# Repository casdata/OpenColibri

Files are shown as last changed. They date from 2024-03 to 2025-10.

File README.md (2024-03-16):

# OpenColibri
Control board for the Necta Colibri vending machine + firmware

The OpenColibri project is an alternative solution for the Colibri - Necta coffee machines with a damaged main board, enabling all the features except for the stirrer dispensing unit and the cup dispenser unit.

The board features an ESP32 MCU, programmed over ESP-IDF. 

There are 13 available recipe slots to program and choose from. The button #8 works as a page changer, when pressed the current page changes, giving access to the rest of the recipe slots. In total, there are 2 pages, seven recipes are available on the first page and six on the second page, in this last one, push button #7 works as a manual hot water outlet switch, pressing it will toggle the hot water outlet.

Button #8 cancels the selected recipe preparation only while the grinder is working, after this, the preparation can’t be canceled.

<p align="center">
  
</p>

## Board
Front            |  Back
:-------------------------:|:-------------------------:
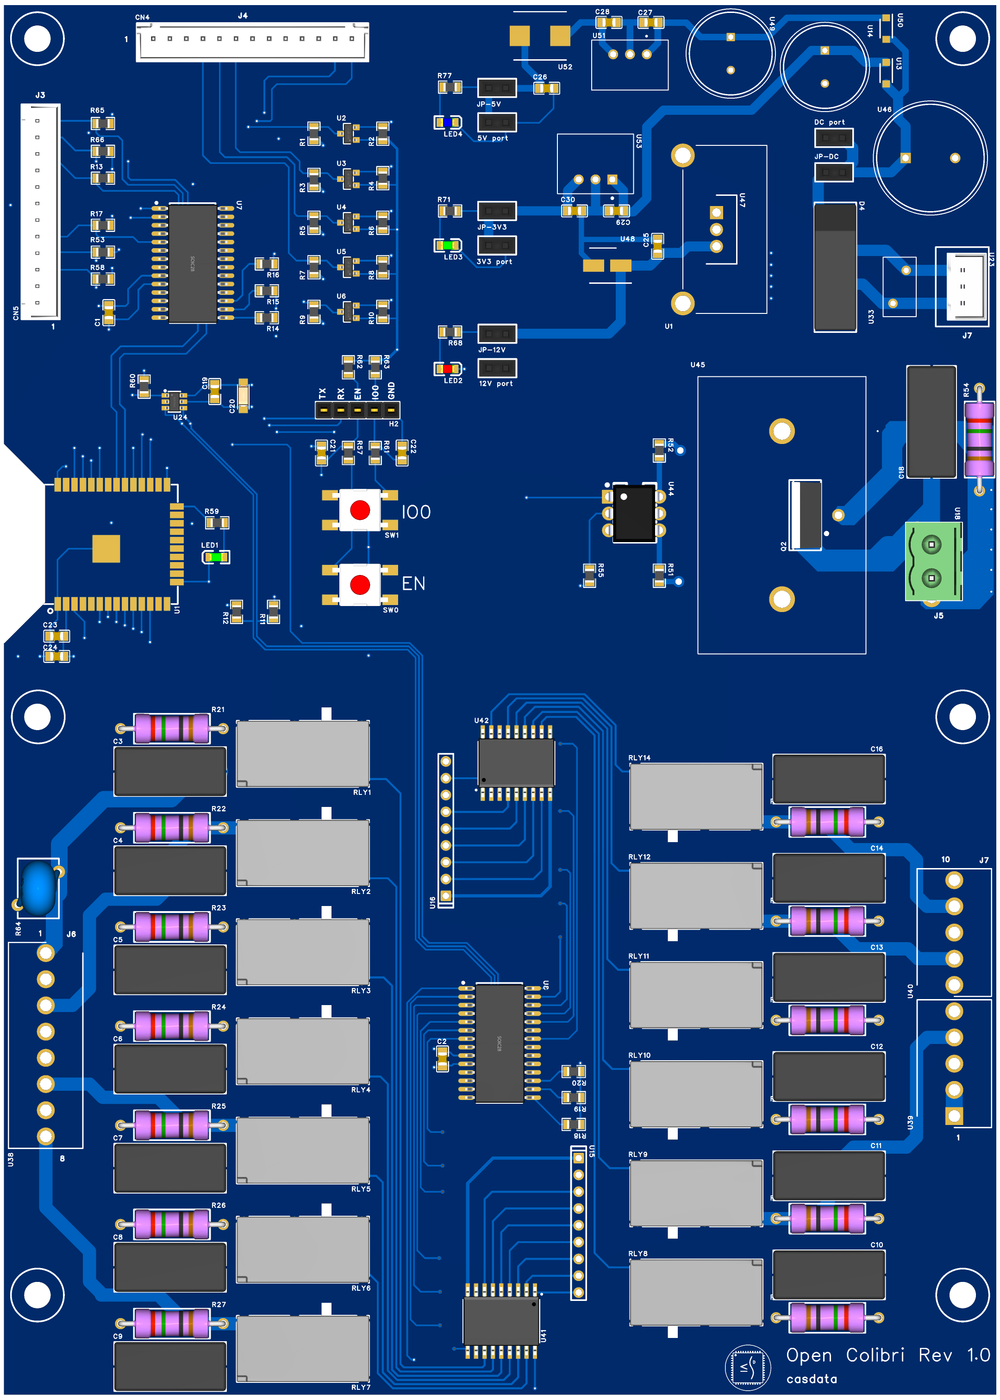
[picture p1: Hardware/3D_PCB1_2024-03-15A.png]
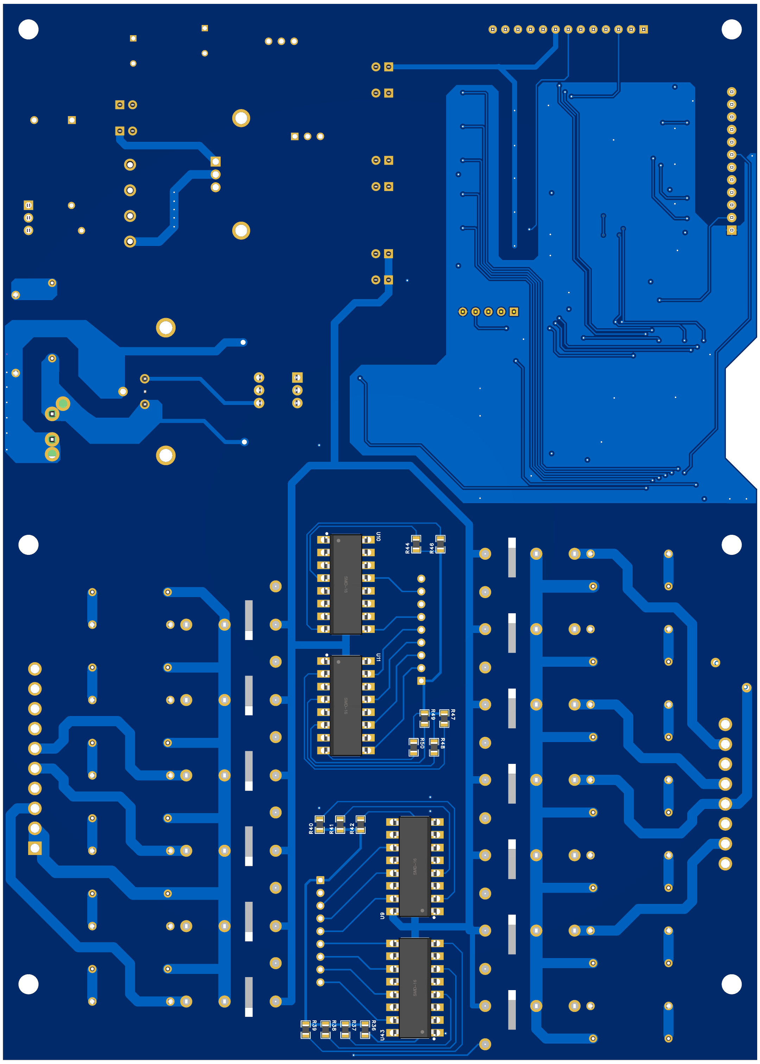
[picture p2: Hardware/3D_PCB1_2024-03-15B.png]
  |  

## Schematic Diagram
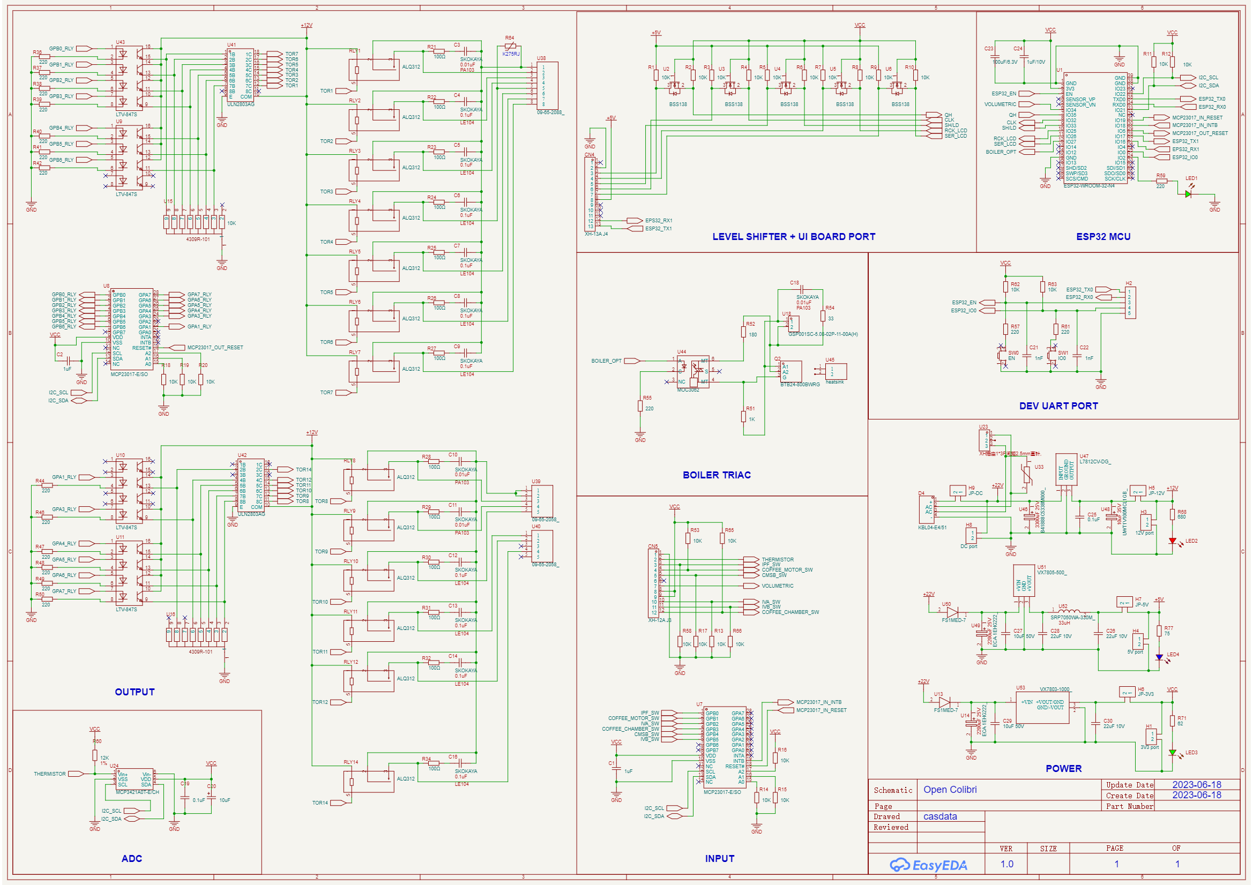
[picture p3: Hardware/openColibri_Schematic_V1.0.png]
Schematic
     

## Android App
To create and assign recipes to the recipe slots, the App “OpenColibri” for Android (Android 12 and lesser) is available for this task, it communicates with the machine through BLE (Bluetooth Low Energy). Download APK <a href="Android App/android-release.apk">Here</a>

  <p align="center">
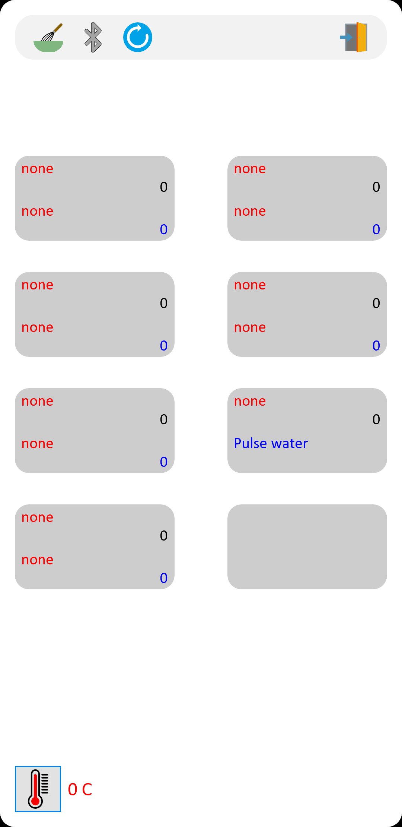
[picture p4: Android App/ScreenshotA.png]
    
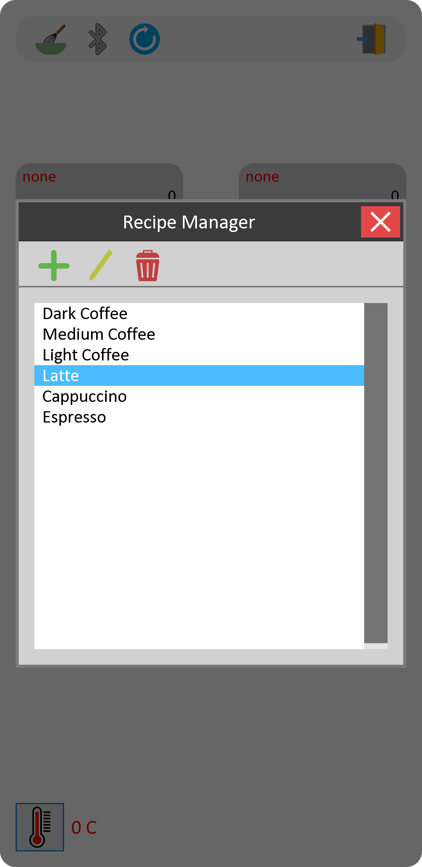
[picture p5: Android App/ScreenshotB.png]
    
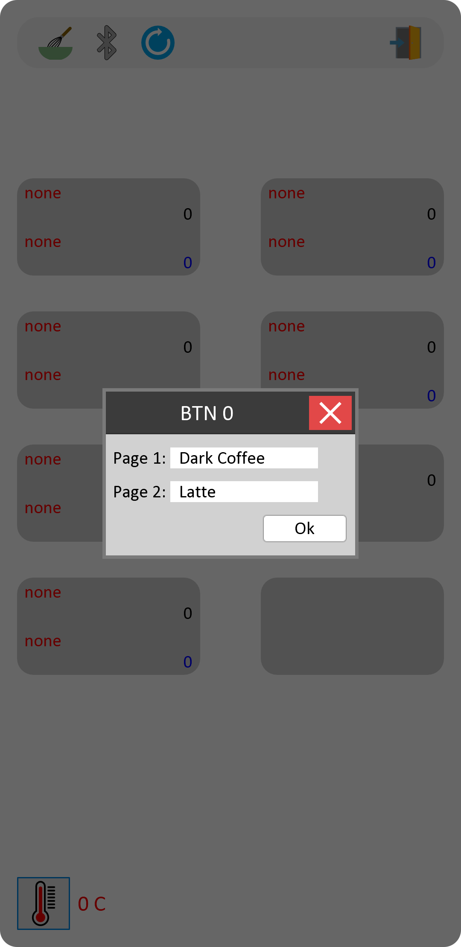
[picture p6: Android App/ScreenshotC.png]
    
  </p>

  The app is in Beta version, it works and it’s functional. It's normal to find some crash bugs. Don’t assign any recipe to the buttons or press the synchronize or boiler buttons before the App and the machine is synchronized, otherwise, it will crash.

  <h3>Connect to the App</h3>
<ul type="1">
  <li>Press the “Washing cycle” button in the machine, and the word “MAINTENANCE” will be displayed, button #1 will enable the BLE of the ESP32, and once pressed, the message “Bluetooth ON” will be displayed.</li>
  <li>Open the App on your Android device, press the Bluetooth icon, connect to the “OpenColibri”, press the synchronize button (the blue circle with the arrow), and wait a few seconds.</li>
  <li>After synchronization is done, any change made in the app will automatically sent to the machine.</li>
</ul>

## Washing Button
The original washing button of the machine is used for a basic maintenance menu, after pressed, it will show "MAINTENANCE" in the display.
<ul>
  <li>Button #1: Enables Bluetooth</li>
  <li>Button #5: Washing cycle</li>
  <li>Button #7: Exit maintenance menu</li>
</ul>

## Contact

Sergio Daniel Castañeda N. - [@twitter_handle](https://twitter.com/CasdataSergio) - casdata@gmail.com

Website: http://casnisoft.weebly.com

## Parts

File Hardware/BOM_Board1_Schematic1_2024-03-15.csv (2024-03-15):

No. | Quantity | Comment | Designator | Footprint | Value | Manufacturer Part | Manufacturer | Supplier Part | Supplier
1 | 2 | 1uF | C1,C2 | C0805 | 1uF
2 | 14 | SKOKAYA | C3,C4,C5,C6,C7,C8,C9,C10,C11,C12,C13,C14,C16,C18 | CAP-TH_L16.9-W7.4-P15.00-D0.6 |  | SKOKAYA |  | C9900019984 | LCSC
3 | 2 | 0.1uF | C19,C25 | C0805 | 0.1uF
4 | 1 | 10uF | C20 | CAP-SMD_L3.2-W1.6-RD-C7171 | 10uF | TAJA106K016RNJ | Kyocera AVX | C7171 | LCSC
5 | 2 | 1nF | C21,C22 | C0805 | 1nF
6 | 1 | 100uF/6.3V | C23 | C0805 | 100uF/6.3V
7 | 1 | 1uF/10V | C24 | C0805 | 1uF/10V
8 | 3 | 22uF 10V | C26,C28,C30 | C0805 | 22uF 10V
9 | 2 | 10uF 50V | C27,C29 | C0805 | 10uF 50V
10 | 1 | XH-13A J4 | CN4 | CONN-TH_13P-P2.50_XH-13A |  | XH-13A | BOOMELE(博穆精密) | C40669 | LCSC
11 | 1 | XH-12A J3 | CN5 | CONN-TH_12P-P2.50_HCTL_XH-12A_C2908610 |  | XH-12A | HCTL(华灿天禄) | C2908610 | LCSC
12 | 1 | KBL04-E4/51 | D4 | KBL_4P-L19.0-W6.3-P5.10 |  | KBL04-E4/51 | VISHAY(威世) | C145346 | LCSC
13 | 1 | 3V3 port | H1 | HDR-TH_2P-P2.54-V-F
14 | 1 | HDR-F_2.54_1x5P | H2 | HDR-TH_5P-P2.54-V-F
15 | 1 | 12V port | H3 | HDR-TH_2P-P2.54-V-F
16 | 1 | 5V port | H4 | HDR-TH_2P-P2.54-V-F
17 | 1 | JP-12V | H5 | HDR-TH_2P-P2.54-V-F
18 | 1 | JP-3V3 | H6 | HDR-TH_2P-P2.54-V-F
19 | 1 | JP-5V | H7 | HDR-TH_2P-P2.54-V-F
20 | 1 | DC port | H8 | HDR-TH_2P-P2.54-V-F
21 | 1 | JP-DC | H9 | HDR-TH_2P-P2.54-V-F
22 | 2 | LED_0805-G | LED1,LED3 | LED0805-RD_GREEN
23 | 1 | LED_0805-R | LED2 | LED0805-RD_GREEN
24 | 1 | LED_0805-B | LED4 | LED0805-RD_GREEN
25 | 1 | BTB24-800BWRG | Q2 | TO-220-3_L10.0-W4.5-P2.54-L |  | BTB24-800BWRG | ST(意法半导体) | C262877 | LCSC
26 | 26 | 10K | R1,R2,R3,R4,R5,R6,R7,R8,R9,R10,R11,R12,R13,R14,R15,R16,R17,R18,R19,R20,R53,R58,R62,R63,R65,R66 | R0805 | 10K
27 | 13 | 100Ω | R21,R22,R23,R24,R25,R26,R27,R28,R29,R30,R31,R32,R34 | RES-TH_BD4.5-L11.5-P15.50-D0.8 | 100Ω
28 | 17 | 220 | R36,R37,R38,R39,R40,R41,R42,R44,R46,R47,R48,R49,R50,R55,R57,R59,R61 | R0805 | 220
29 | 1 | 1K | R51 | R0805 | 1K
30 | 1 | 180 | R52 | R0805 | 180
31 | 1 | 33 | R54 | RES-TH_BD4.5-L11.5-P15.50-D0.8 | 33
32 | 1 | 12K | R60 | R0805 | 12K
33 | 1 | FTR07D781K | R64 | RES-TH_L9.0-W6.2-P5.00-D0.7-S6.20 |  | FTR07D781K | FTR(乔光电子) | C693590 | LCSC
34 | 1 | 680 | R68 | R0805 | 680
35 | 1 | 62 | R71 | R0805 | 62
36 | 1 | 75 | R77 | R0805 | 75
37 | 13 | ALQ312 | RLY1,RLY2,RLY3,RLY4,RLY5,RLY6,RLY7,RLY8,RLY9,RLY10,RLY11,RLY12,RLY14 | RELAY-TH_ALQ3XX |  | ALQ312 | PANASONIC(松下) | C425093 | LCSC
38 | 1 | EN | SW0 | SW-SMD_4P-L6.0-W6.0-P4.50-LS9.0-2
39 | 1 | IO0 | SW1 | SW-SMD_4P-L6.0-W6.0-P4.50-LS9.0-2
40 | 1 | ESP32-WROOM-32-N4 | U1 | WIFIM-SMD_ESP32-WROOM-32-N4 |  | ESP32-WROOM-32-N4 | ESPRESSIF(乐鑫) | C82899 | LCSC
41 | 5 | BSS138 | U2,U3,U4,U5,U6 | SOT-23_L2.9-W1.3-P1.90-LS2.4-BR |  | BSS138 | JUXING(钜兴) | C5279927 | LCSC
42 | 2 | MCP23017-E/SO | U7,U8 | SOIC-28_L18.0-W7.5-P1.27-LS10.3-BL |  | MCP23017-E/SO | MICROCHIP(美国微芯) | C47023 | LCSC
43 | 4 | LTV-847S | U9,U10,U11,U43 | OPTO-SMD-16_L19.8-W6.5-P2.54-LS10.2-BL |  | LTV-847S |  | C9900002565 | LCSC
44 | 2 | FS1MED-7 | U13,U50 | SODFL3718X120N
45 | 2 | 423d72adf0cc4111bf5e44c35dbd3aef | U14,U49 | CAPPRD500W65D1250H2700
46 | 1 | 10K | U15 | 4309R-101 9P 2.54
47 | 1 | 4309R-101 | U16 | 4309R-101 9P 2.54
48 | 1 | GSP001SC-5.08-02P-11-00A(H) | U18 | CONN-TH_2P-P5.08_GOOSVN_GSP001SC-5.08-02P-11-00A |  | GSP001SC-5.08-02P-11-00A(H) | GOOSVN(高胜) | C5223769 | LCSC
49 | 1 | XH插座1*3P间距2.5mm直针, | U23 | CONN-TH_C722693 |  | XH插座1*3P间距2.5mm直针, |  | C9900015994 | LCSC
50 | 1 | MCP3421A0T-E/CH | U24 | SOT-23-6_L2.9-W1.6-P0.95-LS2.8-BR |  | MCP3421A0T-E/CH | MICROCHIP(美国微芯) | C29454 | LCSC
51 | 1 | V22ZA1P | U33 | V22ZA1P
52 | 1 | 6dd98926c4964025bade0356167c3037 | U38 | SHDR8W160P0X396_1X8_3092X1062X
53 | 2 | 0ef649be63f348d9a9fb1e8e0b13fae2 | U39,U40 | HDRV5W80P0X396_1X5_1904X1062X1
54 | 2 | ULN2803AG | U41,U42 | SOP-18_L11.5-W7.5-P1.27-LS10.3 |  | ULN2803AG | LANKE(兰科) | C2828556 | LCSC
55 | 1 | MOC3062 | U44 | PDIP-6_L8.5-W6.5-P2.54-LS7.6-BL |  | MOC3062 | LITEON(光宝) | C115473 | LCSC
56 | 1 | heatsink | U45 | 65715ABPE
57 | 1 | f1ad3a9c3df647b5ae5f0771636e6a53 | U46 | CAPPRD750W85D1625H3350
58 | 1 | ed5773b1048145188ff2be5e021da6e6 | U47 | TO255P460X1020X2008-3P
59 | 1 | c534dcd06943492eb338f11ed3634518 | U48 | CAPAE530X550N
60 | 1 | 4b0cc18e117e430396a12b9f0bba2d3b | U51 | VX7805500
61 | 1 | 09b60b7cccee4037ae637b1b8858bb9a | U52 | INDPM7973X540N
62 | 1 | 68940f397d494c0f9dc5991943d3ca98 | U53 | VX78012-1000_VX7803-1000

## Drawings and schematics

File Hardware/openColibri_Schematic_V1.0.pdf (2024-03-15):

# COM 10 8C 11 7C 12 6C 13 5C 14 4C 15 3C 16 2C 17 1C 18

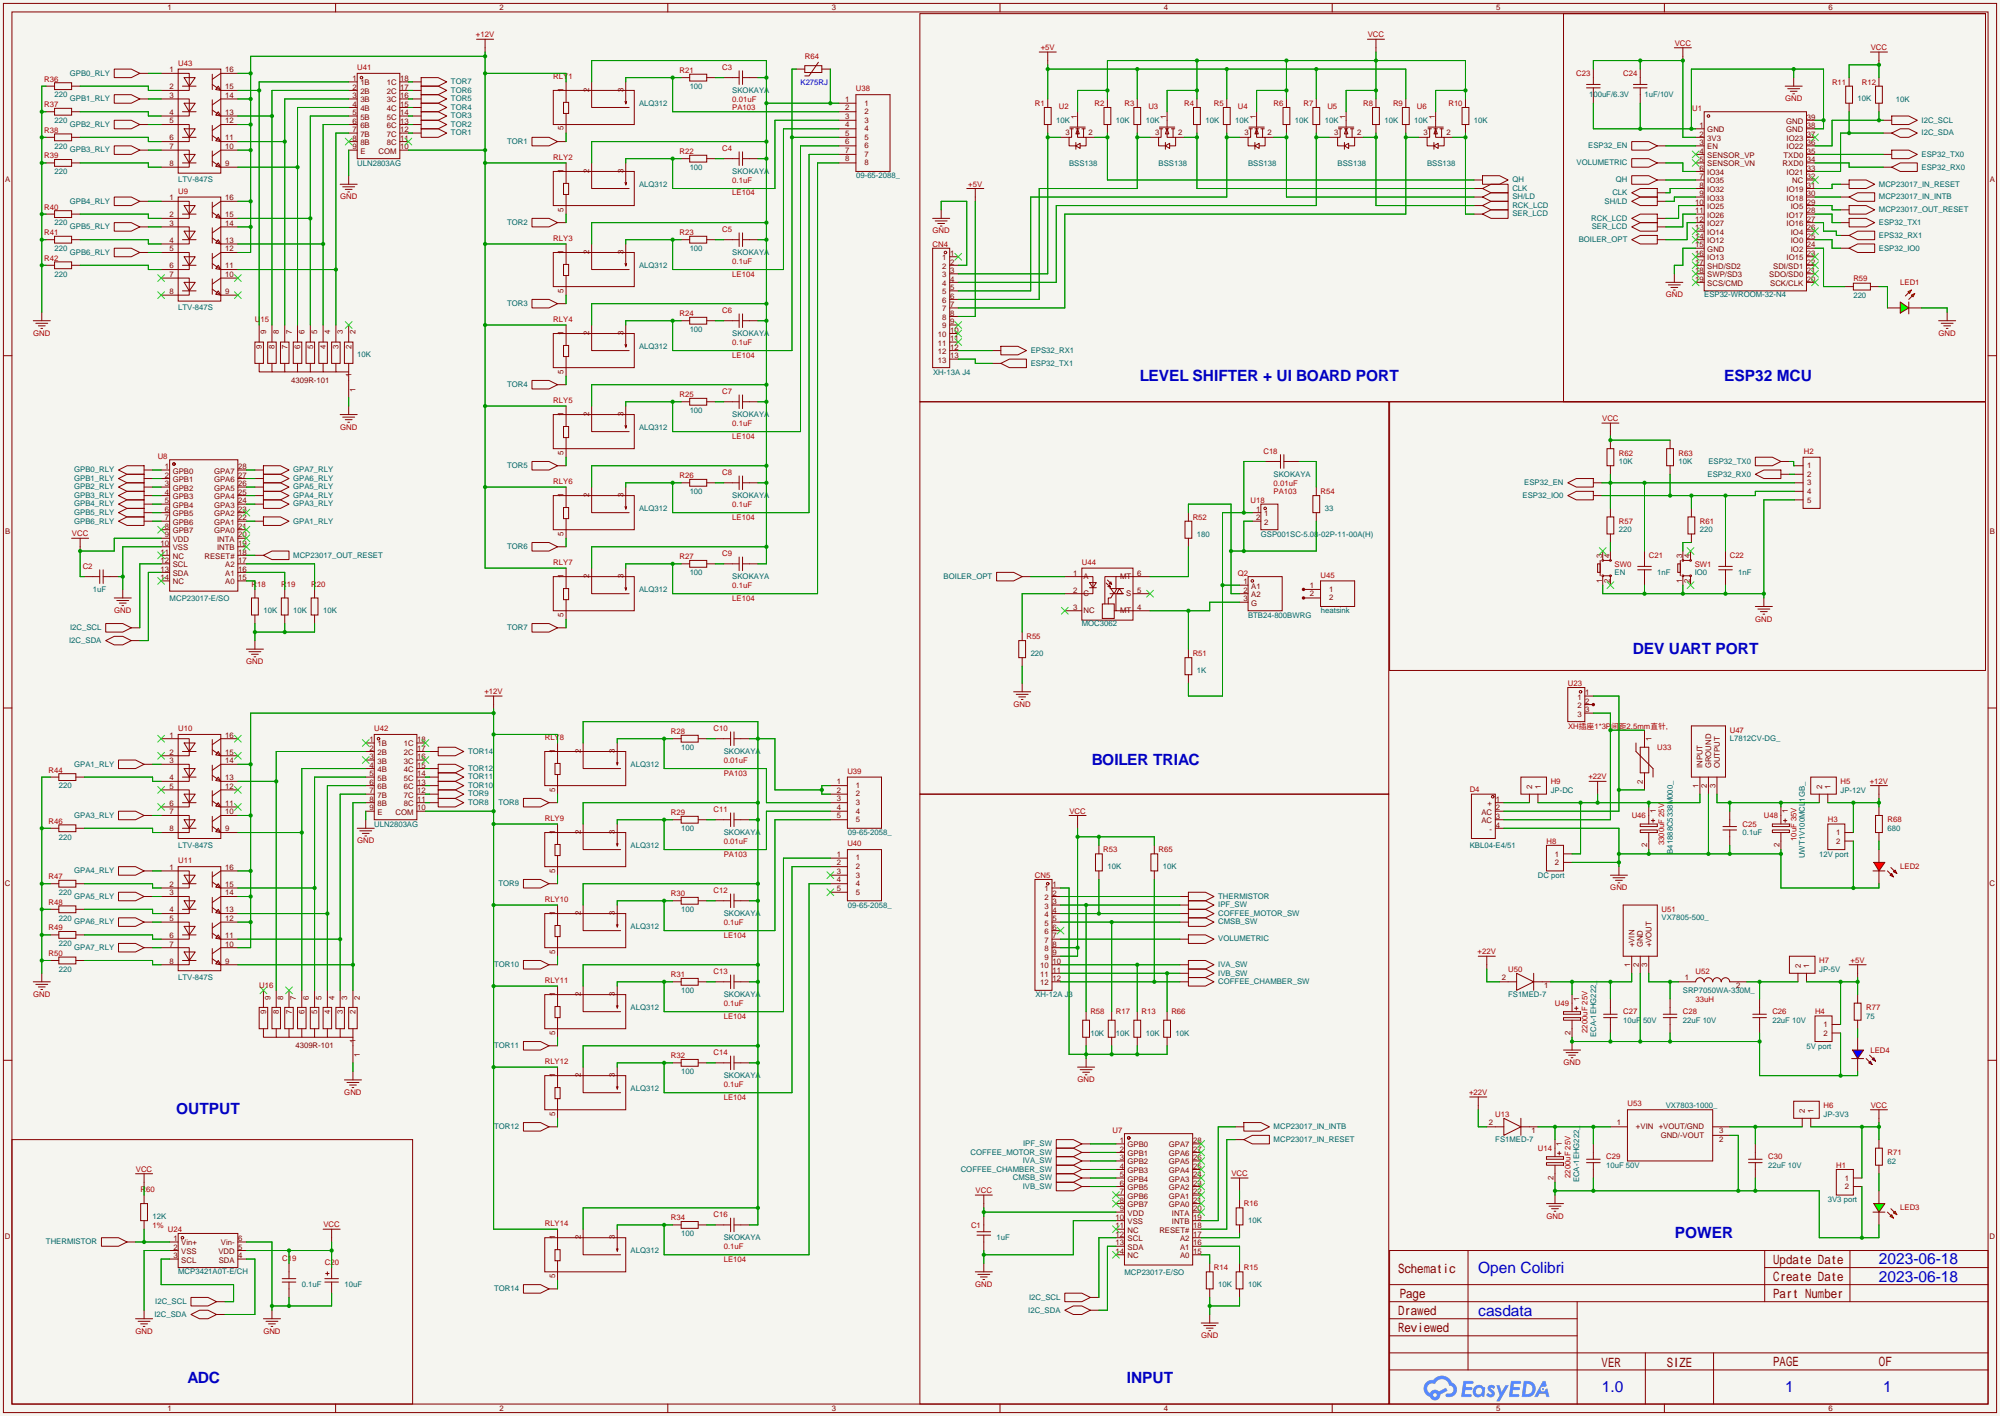
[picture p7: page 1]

LEVEL SHIFTER + UI BOARD PORT

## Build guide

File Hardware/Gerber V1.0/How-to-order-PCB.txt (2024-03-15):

How to Order PCB

Please refer to:
https://prodocs.easyeda.com/en/pcb/order-order-pcb/index.html

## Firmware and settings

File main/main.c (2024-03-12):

#include "extend.h"
#include "controlT.h"
#include "uiT.h"
#include "boilerT.h"
#include "interruptsT.h"


QueueHandle_t xQueueIntB = NULL;
QueueHandle_t xQueueInputsSw = NULL;
QueueHandle_t xQueueInputBtns = NULL;
QueueHandle_t xQueueInputPulse = NULL;
QueueHandle_t xQueueInputTimePerPulse = NULL;
QueueHandle_t xQueueBoilerTemp = NULL;
QueueHandle_t xQueueUI = NULL;
QueueHandle_t xQueueData2Boiler = NULL;



static void IRAM_ATTR interrupt_handler(void *args){
    int16_t pinNumber = (int16_t)args;
    xQueueSendFromISR(xQueueIntB, &pinNumber, NULL);
    //ESP_LOGI("INTR", "Interrupt intb %d", pinNumber);
}


static void initQueues(){
    xQueueIntB = xQueueCreate(10, sizeof(int16_t));
    xQueueInputsSw = xQueueCreate(1, sizeof(InputSwStruct));
    xQueueInputBtns = xQueueCreate(1, sizeof(InputBtnStruct));
    xQueueInputPulse = xQueueCreate(1, sizeof(uint16_t));
    xQueueInputTimePerPulse = xQueueCreate(1, sizeof(double));
    xQueueBoilerTemp = xQueueCreate(1, sizeof(float));
    xQueueUI = xQueueCreate(5, sizeof(UiData));
    xQueueData2Boiler = xQueueCreate(5, sizeof(uint8_t));

    if(xQueueIntB == NULL)
        ESP_LOGE(MAIN_TASK_TAG, "xQueueIntB initialization error!");
    
    if(xQueueInputsSw == NULL)
        ESP_LOGE(MAIN_TASK_TAG, "xQueueInputsSw initialization error!");

    if(xQueueInputBtns == NULL)
        ESP_LOGE(MAIN_TASK_TAG, "xQueueInputBtns initialization error!");

    if(xQueueInputPulse == NULL)
        ESP_LOGE(MAIN_TASK_TAG, "xQueueInputPulse initialization error!");

    if(xQueueInputTimePerPulse == NULL)
        ESP_LOGE(MAIN_TASK_TAG, "xQueueInputTimePerPulse initialization error!");

    if(xQueueUI == NULL)
        ESP_LOGE(MAIN_TASK_TAG, "xQueueUI initialization error!");

    if(xQueueData2Boiler == NULL)
        ESP_LOGE(MAIN_TASK_TAG, "xQueueData2Boiler initialization error!");

    if(xQueueBoilerTemp == NULL)
        ESP_LOGE(MAIN_TASK_TAG, "xQueueBoilerTemp initialization error!");



}

static void initGPIO(){
    gpio_reset_pin(CLK_UI_PIN);
    gpio_reset_pin(SH_LD_UI_PIN);
    gpio_reset_pin(IN_SERIAL_UI_PIN);
    gpio_reset_pin(RCK_DISPLAY_PIN);
    gpio_reset_pin(SER_DISPLAY_PIN);
    gpio_reset_pin(MCP23017_IN_RS_PIN);
    gpio_reset_pin(MCP23017_OUT_RS_PIN);
    gpio_reset_pin(MCP23017_INTB_PIN);
    gpio_reset_pin(VOLUMETRIC_PIN);
    gpio_reset_pin(BOILER_PIN);
    gpio_reset_pin(STATUS_LED_PIN);


    gpio_set_direction(CLK_UI_PIN, GPIO_MODE_OUTPUT);
    gpio_set_direction(SH_LD_UI_PIN, GPIO_MODE_OUTPUT);
    gpio_set_direction(RCK_DISPLAY_PIN, GPIO_MODE_OUTPUT);
    gpio_set_direction(SER_DISPLAY_PIN, GPIO_MODE_OUTPUT);
    gpio_set_direction(MCP23017_IN_RS_PIN, GPIO_MODE_OUTPUT);
    gpio_set_direction(MCP23017_OUT_RS_PIN, GPIO_MODE_OUTPUT);
    gpio_set_direction(BOILER_PIN, GPIO_MODE_OUTPUT);
    gpio_set_direction(STATUS_LED_PIN, GPIO_MODE_OUTPUT);

    gpio_set_direction(MCP23017_INTB_PIN, GPIO_MODE_INPUT);
    gpio_set_direction(IN_SERIAL_UI_PIN, GPIO_MODE_INPUT);
    gpio_set_direction(VOLUMETRIC_PIN, GPIO_MODE_INPUT);
    
    gpio_set_intr_type(MCP23017_INTB_PIN, GPIO_INTR_POSEDGE);
    gpio_set_intr_type(VOLUMETRIC_PIN, GPIO_INTR_POSEDGE);

    gpio_install_isr_service(0);
    gpio_isr_handler_add(MCP23017_INTB_PIN, interrupt_handler, (void *)MCP23017_INTB_PIN);
    gpio_isr_handler_add(VOLUMETRIC_PIN, interrupt_handler, (void *)VOLUMETRIC_PIN);


    gpio_set_level(CLK_UI_PIN, 1);
    gpio_set_level(SH_LD_UI_PIN, 0);
    gpio_set_level(RCK_DISPLAY_PIN, 1);
    gpio_set_level(SER_DISPLAY_PIN, 1);
    gpio_set_level(MCP23017_IN_RS_PIN, 1);
    gpio_set_level(MCP23017_OUT_RS_PIN, 1);
    //gpio_set_level(BOILER_PIN, 0);
    gpio_set_level(STATUS_LED_PIN, 0);

    if(!NEXTION_LCD){
        gpio_reset_pin(POWDER_C_PIN);

        gpio_set_direction(POWDER_C_PIN, GPIO_MODE_OUTPUT);

        gpio_set_level(POWDER_C_PIN, 0);
    }
}

static void initI2C(){

    int i2c_port = I2C_PORT_NUM;

    i2c_config_t i2cConfig = {
        .mode = I2C_MODE_MASTER,
        .sda_io_num = I2C_SDA_PIN,
        .scl_io_num = I2C_SCL_PIN,
        .sda_pullup_en = GPIO_PULLUP_ENABLE,
        .scl_pullup_en = GPIO_PULLUP_ENABLE,
        .master.clk_speed = I2C_FREQ_HZ
    };

    i2c_param_config(i2c_port, &i2cConfig);

    ESP_ERROR_CHECK(i2c_driver_install(i2c_port, i2cConfig.mode, I2C_RX_BUFF_DISABLE, I2C_TX_BUFF_DISABLE, 0));

}

static void initLEDC(){

    ledc_timer_config_t ledcConfig = {
        .speed_mode       = LEDC_LOW_SPEED_MODE,
        .timer_num        = LEDC_TIMER_0,
        .duty_resolution  = LEDC_TIMER_13_BIT,
        .freq_hz          = 1000,
        .clk_cfg          = LEDC_AUTO_CLK
    };

    ESP_ERROR_CHECK(ledc_timer_config(&ledcConfig));

    ledc_channel_config_t ledcChannel = {
        .speed_mode     = LEDC_MODE,
        .channel        = LEDC_CHANNEL,
        .timer_sel      = LEDC_TIMER,
        .intr_type      = LEDC_INTR_DISABLE,
        .gpio_num       = BOILER_PIN,//STATUS_LED_PIN,       //BOILER_PIN
        .duty           = 0,
        .hpoint         = 0
    };

    ESP_ERROR_CHECK(ledc_channel_config(&ledcChannel));

}

static void initNextion(){
    const uart_config_t uart_config = {
        .baud_rate = 9600,
        .data_bits = UART_DATA_8_BITS,
        .parity = UART_PARITY_DISABLE,
        .stop_bits = UART_STOP_BITS_1,
        .flow_ctrl = UART_HW_FLOWCTRL_DISABLE,
        .source_clk = UART_SCLK_DEFAULT
    };

    ESP_ERROR_CHECK(uart_driver_install(UART_PORT_N, BUFF_SIZE * 2, BUFF_SIZE * 2, 10, &xQueueUart, 0));
    ESP_ERROR_CHECK(uart_param_config(UART_PORT_N, &uart_config));
    ESP_ERROR_CHECK(uart_set_pin(UART_PORT_N, TXD_2_PIN, RXD_2_PIN, UART_PIN_NO_CHANGE, UART_PIN_NO_CHANGE));
    ESP_ERROR_CHECK(uart_enable_pattern_det_baud_intr(UART_PORT_N, NEXTION_D_CHAR, 1, 9, 0, 0));
    ESP_ERROR_CHECK(uart_pattern_queue_reset(UART_PORT_N, 10));
}

static void initPID(){
    
}

static void initNVS(){
    esp_err_t err = nvs_flash_init();

    if(err != ESP_OK){
        ESP_LOGI(MAIN_TASK_TAG, "nvs flash init error");
        return;
    }
}


void app_main(void)
{

    initQueues();

    initGPIO();
    initI2C();
    initLEDC();

    if(NEXTION_LCD)
        initNextion();

    initPID();
    initNVS();

    initI2C_MCP23017_Out();
    initI2C_MCP23017_In();

    initControlTask();
    initUiTask();
    initBoilerTask();
    initInterruptsTask();


}

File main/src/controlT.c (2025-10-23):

#include "controlT.h"
#define FIXED


TaskHandle_t controlTaskH = NULL;

static struct gatts_profile_inst spp_profile_tab[SPP_PROFILE_NUM] = {
    [SPP_PROFILE_APP_IDX] = {
        .gatts_cb = gatts_profile_event_handler,
        .gatts_if = ESP_GATT_IF_NONE,       /* Not get the gatt_if, so initial is ESP_GATT_IF_NONE */
    },
};

/*
 *  SPP PROFILE ATTRIBUTES
 ****************************************************************************************
 */

#define CHAR_DECLARATION_SIZE   (sizeof(uint8_t))
static const uint16_t primary_service_uuid = ESP_GATT_UUID_PRI_SERVICE;
static const uint16_t character_declaration_uuid = ESP_GATT_UUID_CHAR_DECLARE;
static const uint16_t character_client_config_uuid = ESP_GATT_UUID_CHAR_CLIENT_CONFIG;

static const uint8_t char_prop_read_notify = ESP_GATT_CHAR_PROP_BIT_READ|ESP_GATT_CHAR_PROP_BIT_NOTIFY;
static const uint8_t char_prop_read_write = ESP_GATT_CHAR_PROP_BIT_WRITE_NR|ESP_GATT_CHAR_PROP_BIT_READ;

///SPP Service - data receive characteristic, read&write without response
static const uint16_t spp_data_receive_uuid = ESP_GATT_UUID_SPP_DATA_RECEIVE;
static const uint8_t  spp_data_receive_val[20] = {0x00};

///SPP Service - data notify characteristic, notify&read
static const uint16_t spp_data_notify_uuid = ESP_GATT_UUID_SPP_DATA_NOTIFY;
static const uint8_t  spp_data_notify_val[20] = {0x00};
static const uint8_t  spp_data_notify_ccc[2] = {0x00, 0x00};

bool sendNextData;
SyncroState syncroState;
char *recvBuff;
char *commandBuff;
Recipe *recipeList;

///Full HRS Database Description - Used to add attributes into the database
static const esp_gatts_attr_db_t spp_gatt_db[SPP_IDX_NB] =
{
    //SPP -  Service Declaration
    [SPP_IDX_SVC]                      	=
    {{ESP_GATT_AUTO_RSP}, {ESP_UUID_LEN_16, (uint8_t *)&primary_service_uuid, ESP_GATT_PERM_READ,
    sizeof(spp_service_uuid), sizeof(spp_service_uuid), (uint8_t *)&spp_service_uuid}},

    //SPP -  data receive characteristic Declaration
    [SPP_IDX_SPP_DATA_RECV_CHAR]            =
    {{ESP_GATT_AUTO_RSP}, {ESP_UUID_LEN_16, (uint8_t *)&character_declaration_uuid, ESP_GATT_PERM_READ,
    CHAR_DECLARATION_SIZE,CHAR_DECLARATION_SIZE, (uint8_t *)&char_prop_read_write}},

    //SPP -  data receive characteristic Value
    [SPP_IDX_SPP_DATA_RECV_VAL]             	=
    {{ESP_GATT_AUTO_RSP}, {ESP_UUID_LEN_16, (uint8_t *)&spp_data_receive_uuid, ESP_GATT_PERM_READ|ESP_GATT_PERM_WRITE,
    SPP_DATA_MAX_LEN,sizeof(spp_data_receive_val), (uint8_t *)spp_data_receive_val}},

    //SPP -  data notify characteristic Declaration
    [SPP_IDX_SPP_DATA_NOTIFY_CHAR]  =
    {{ESP_GATT_AUTO_RSP}, {ESP_UUID_LEN_16, (uint8_t *)&character_declaration_uuid, ESP_GATT_PERM_READ,
    CHAR_DECLARATION_SIZE,CHAR_DECLARATION_SIZE, (uint8_t *)&char_prop_read_notify}},

    //SPP -  data notify characteristic Value
    [SPP_IDX_SPP_DATA_NTY_VAL]   =
    {{ESP_GATT_AUTO_RSP}, {ESP_UUID_LEN_16, (uint8_t *)&spp_data_notify_uuid, ESP_GATT_PERM_READ,
    SPP_DATA_MAX_LEN, sizeof(spp_data_notify_val), (uint8_t *)spp_data_notify_val}},

    //SPP -  data notify characteristic - Client Characteristic Configuration Descriptor
    [SPP_IDX_SPP_DATA_NTF_CFG]         =
    {{ESP_GATT_AUTO_RSP}, {ESP_UUID_LEN_16, (uint8_t *)&character_client_config_uuid, ESP_GATT_PERM_READ|ESP_GATT_PERM_WRITE,
    sizeof(uint16_t),sizeof(spp_data_notify_ccc), (uint8_t *)spp_data_notify_ccc}},

};

static void addRecipeIndex2CommandBuff(uint8_t recipeIndex){

    char *tempData = (char *)malloc(8);

    sprintf(tempData, "%d", recipeIndex);

    if(recipeIndex < 10)
        strcat(commandBuff,"0");

    strcat(commandBuff, tempData);


    free(tempData);

}

static void addU8Value2CommandBuff(uint8_t u8Value){

    char *tempData = (char *)malloc(6);

    memset(tempData, 0, 6);

    sprintf(tempData, "%d", u8Value);

    strcat(commandBuff, tempData);

    free(tempData);

}

static void addU16Value2CommandBuff(uint16_t u16Value){

    char *tempData = (char *)malloc(16);

    memset(tempData, 0, 16);

    sprintf(tempData, "%d", u16Value);

    strcat(commandBuff, tempData);

    free(tempData);

}

static void sendAllRecipes(Recipe *recipe){
    static uint8_t tempPC = 0;
    static uint8_t recipeIndex = 0;
    static bool createCommand = true;


    if(sendNextData){
        sendNextData = false;
    
        if(createCommand){
            createCommand = false;

            memset(commandBuff, 0, 64);

            strcat(commandBuff, "#");

            size_t modSize = recipe[recipeIndex].moduleSize;

            if(modSize > 0){
                strcat(commandBuff, "d");
                addRecipeIndex2CommandBuff(recipeIndex);

                strcat(commandBuff, recipe[recipeIndex].recipeName);

                strcat(commandBuff, "|o");

                addU16Value2CommandBuff(recipe[recipeIndex].recipeCounter);

                strcat(commandBuff, "|");
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

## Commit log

2023-08-06 - Testing relay outputs 1/2
2023-08-08 - Test on relay outputs 2/2
2023-08-09 - Adding thermistor reading 1/2
2023-08-14 - Added thermistor reading - Fully implemented LCD 1601 driver.
2023-08-22 - Fixed project structure - Added control and interrupts task
    [boilerT.c, controlT.c, extend.h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]
2023-08-29 - Added queue for boiler temperature - Added airbreak check at booting in the control task - Added error states in the ui task
    [boilerT.c, controlT.c, extend.h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]
2023-09-05 - Added PWM for boiler pin - Added UI boiler display
2023-10-25 - Added UART feature - Added Nextion PID Tunner connection - Added PID controller in the Boiler task
2023-10-28 - Added pulse counter in the interrupt task - Added PID controller in the boiler task - Added brewer arm and inject functions in the control task.
2024-02-01 - Working on powder algorithm 1/n - Fixed ui page bug.
    [controlT.c, uiT.c]
2024-03-15 - Final Version 011 - Added visual data update message. - Fixed manual water pulse counter bug - Fixed minor display bugs
    [controlT.c, interruptsT.c, uiT.c]
2024-03-15 Added Hardware folder
    [BOM_Board1_Schematic1_2024-03-15.csv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]
2025-10-10 Back to Fixed Bug commit
    [controlT.c, extend.h, interruptsT.c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]
2025-10-11 Fixed airbreak water overflow after a drink was dispensed.
    [controlT.c, extend.h, interruptsT.c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]
2025-10-21 - Added water overflow failsafe.
    [interruptsT.c, uiT.c]
2025-10-21 - Boiler temperature displayed on idle mode.
2026-02-08 - Version 018c - Auto exit of page 2. - Added low pass filter to the temperature value. - Working on temp control 1/n
